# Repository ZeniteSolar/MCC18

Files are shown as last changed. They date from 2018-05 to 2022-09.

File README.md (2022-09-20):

# MCC18
Solar panel MPPT, cuk converter, with microcontroller 

# Procedimento de testes - MCC18

 - [Inspeção](#inspeção)
 - [Disgnostico Inicial](#diagnóstico-inicial)
 - [Diagnostico Preventivo](#diagnostico-preventivo)
 - [Teste Geral](#teste-geral)
    - [Entrada e saída de potencia](#entrada-e-saída-da-potência)
    - [Funcional](#funcional)
 - [Testes Individuais](#testes-individuais)
    - [Signals](#signals)
    - [MCC CAN Shield](#mcccanshield) 
 - [Driver](#driver)
    - [Esquematico](#esquemático)
    - [Reparos Obrigatorios](#reparos-obrigatórios)
    - [Verificando funcionamento](#verificando-se-está-funcionando)
    - [Correção de falhas](#correção-de-falhas)
        - [Se não houver sinal retangular na saída](#se-não-houver-sinal-retangular-na-saída)
        - [Se não houver +15V e -5V](#se-não-houver-15v-e--5v)
        - [Se não houver tensão em um dos barramentos de +15V ou -5V](#se-não-houver-tensão-em-um-dos-barramentos-de-15v-ou--5v)
        - [Se tem tensão no barramento, mas não tem sinal em gate e source](#se-tem-tensão-no-barramento-mas-não-tem-sinal-em-gate-e-source)

**Importante**: 
<span style="color:red">
NÃO TROCAR COMPONENTES ENTRE AS PLACAS, CADA MCC TEM SEU MCC_CAN_SHIELD, E CADA MCC_CAN_SHIELD TEM  SEU ATMEGA! 
SOMENTE REGRAVAR FIRMWARE EM ÚLTIMO CASO!
SEMPRE USAR LIMITE DE CORRENTE NAS FONTES!
SEMPRE LIMPAR EM BAIXO DO PLÁSTICO DOS CONECTORES BARRA_PINO!
</span>

Também Importante: Esse documento está escrito em ordem sequencial de testes, deve ser lido atentamente, pois um procedimento errado poderá causar danos permanentementes ao sistema, e as vezes difíceis de serem compreendidos.

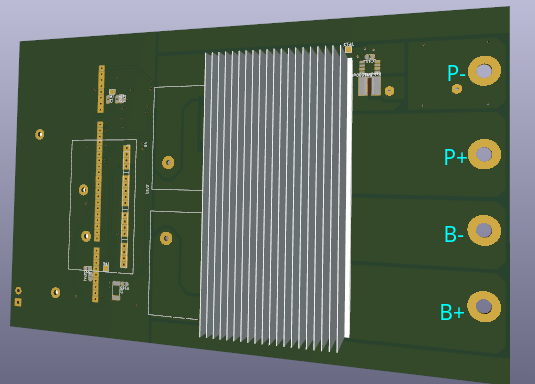
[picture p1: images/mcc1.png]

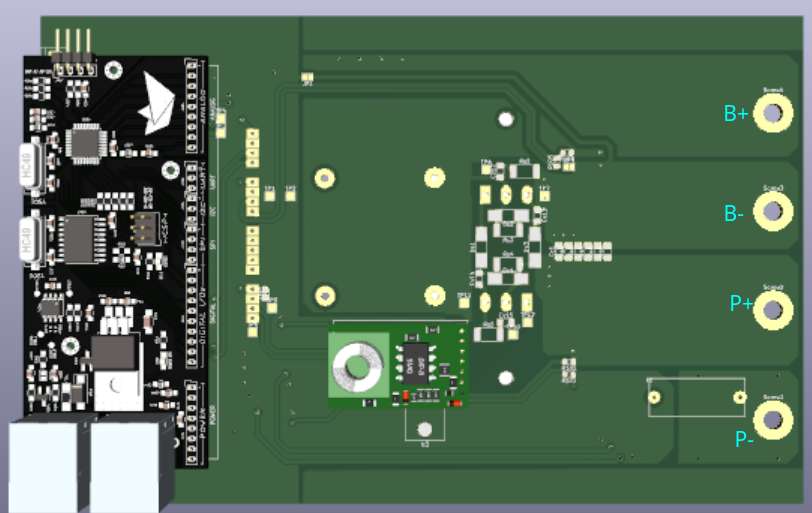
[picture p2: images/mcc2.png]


## INSPEÇÃO
Antes de mais nada, limpeza com álcool e escova, mas especialmente em baixo das barras de pino, pois costumam acumular sujeira em baixo, entre o plástico preto e o cobre, eles podem ser levantados/retirados com uma pinça, fazendo uma alavanca, ou com um alicate universal.
Inspeção visual na placa inteira, especialmente por resíduos e manchas, que podem dar dica sobre onde pode existir problemas. Outro ponto de se observar são trilhas rompidas, componentes rachados ou com aspecto estranho.

## DIAGNÓSTICO INICIAL
Desconectar MCC_CAN_SHIELD, SIGNALS e DRIVER, bem como qualquer elemento externo a placa, como fontes de tensão.

Multímetro: entre B+ e P-, resistência dos indutores, na faixa de mOhms, se tiver alta impedância:
 - Um dos indutores em aberto
 - Shunt em aberto

Multímetro: entre P+ e P-, observar a carga do capacitor, um curto pode ser:
 - Capacitor do painel em curto
 - Mosfet em curto drain-source
 - Capacitor de acoplamento e diodo em curto
 - Capacitor de acoplamento e capacitor da bateria em curto

Multímetro: entre B+ e B-, observar a carga do capacitor, um curto pode ser:
 - Capacitor da bateria em curto
 - Diodo em curto
 - Capacitor de acoplamento em curto
 - Capacitor de acoplamento e capacitor do painel em curto

Multímetro: entre P+ e B-, observar a carga do capacitor de acoplamento, um curto pode ser:
 - Capacitor de acoplamento em curto
 - Diodo e Mosfet em curto

Multímetro: verificar se gate-source ou gate-drain não estão em curto.

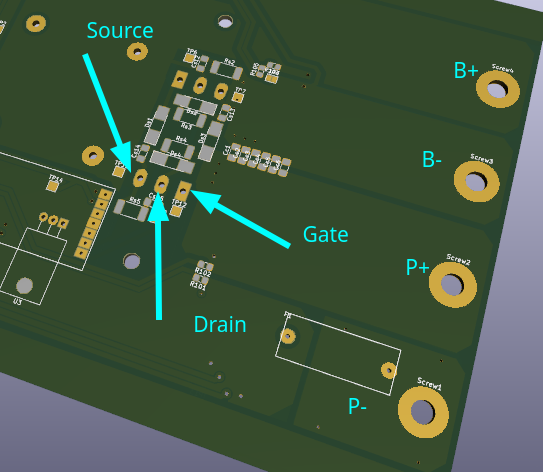
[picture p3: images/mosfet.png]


## DIAGNOSTICO PREVENTIVO

IMPORTANTE, este diagnostico SOMENTE pode ser feito quando se tem certeza de que não houve um mal funcionamento do modulo, por exemplo o modulo ficou em repouso por um tempo e quer verificar o funcionamento. Este teste estima que o modulo não tem nenhuma falha destrutiva, se houver duvidas é recomendável fazer o diagnostico inicial e teste geral antes!!!.

ATENÇÃO! Nunca efetuar o teste sem resistor de carga entre B+ e B- se em algum momento houver a desconexão do mesmo pode danificar o modulo!

 - Ligar uma Fonte CAN a uma fonte de laboratorio com a tensão entre 18 e 30V, limitada em 0.05A e verificar o consumo, se a fonte limitar em corrente examinar o MCC_CAN_Shield está queimado, se não limitar em corrente esperar uns segundos e os leds deveriam piscar alternadamente (talvez passado um tempo um led fique fixo e outro desligado, não tem problema), se não o MCC_CAN_Shield está com problema.
 
 **(Sempre que for ligar uma placa no MCC desligar a fonte CAN (Se estiver usando uma fonte de laboratorio não desligue ela, desconecte o fio que alimenta o circuito é mais seguro))**

 - Com o MCC_CAN_Shield funcionando conecta-lo no MCC e aumentar o limite de corrente da fonte para 0.10A.
 - Conectar o driver e verificar o consumo, se limitar em corrente o driver está queimado, se não prosseguir.
 - Conectar a placa dos sensores, se limitar em corrente a placa está queimada, se não prosseguir.
 - **PASSO MUITO IMPORTANTE** Conectar o resistor de carga (valor máximo: 25R, recomendável: 20R, mínimo: 1R) entre B+ e B-
 - Ligar outra fonte (deve estar isolada) com a tensão em 0V e a corrente limitada a 0.05A entre +P e -P.
 - Medir a tensão de saída
 - Fazer uma rampa na fonte conectada em P+ e P- de 0V até 7V e de 0.05A até 1A (fazer devagar), enquanto faz a rampa a tensão de saída deveria aumentar se não aumentar e a fonte sempre ficar limitando em corrente, tem problema na parte de potencia, se a tensão de saída não aumentar e não houver consumo ou o driver ou a parte de potencia não funcionam
 - Se houve tensão na saída, a fonte de P+ e P- deveria ficar oscilando entre limite de corrente e limite de tensão e os LEDs da placa de controle deveriam estar alternando. Se não for o caso, desconectar o cabo RJ45 e conectar novamente, se mesmo assim depois de uns 30 segundos não ficar oscilando entre o limite de corrente e o limite de tensão, provavelmente algum sensor deve estar queimado.
 - Para diagnosticar o sensor conectar um Arduíno nos pinos de dados e na serial verificar se os valores medidos condizem com os que aparecem na fonte de P+ e P-.

## TESTE GERAL
Primeiro teste a ser realizado após limpeza e inspeção visual. Esse teste garante que as chaves e capacitores de potência estejam sem fuga de corrente para os níveis de tensão de trabalho nominal. Caso haja fuga de corrente, pode-se optar por aumentar o nível da corrente e localizar a fuga pela elevação de temperatura. 

<span style="color:red"> Importante: Obrigatório o uso de óculos de proteção.</span>

### Entrada e Saída da potência

Nesta etapa testamos o isolamento da placa, a capacidade dos capacitores de suportar a tensão, bem como dos indutores, trilhas, fusível e shunt de suportar a corrente.

 - Desenconectar o MCC_CAN_SHIELD, DRIVER e SIGNALS
 - Fazer uma rampa de tensão de 0 a 50V @ 100mA entre B+ e B-
 - Fazer uma rampa de tensão de 0 a 30V @ 100mA entre P+ e P-
 - Fazer uma rampa de tensão de 0 a 100V @ 100mA entre P+ e B-
 - Fazer uma rampa de corrente de 0 a 10A @ 1V entre B+ e P-

### Funcional
**Alimentação e CIs possivelmente vivos**

 - Remover o atmega do MCC_CAN_SHIELD
 - Conectar o MCC_CAN_SHIELD, ligar o cabo CAN, verificar baixo consumo
 - Medir tensão de 5V

**Geração de PWM e sinal de vida**

 - Conectar o atmega no MCC_CAN_SHIELD
 - Conectar o conector da rede CAN, verificar baixo consumo de corrente
 - Conectar USB/SERIAL para monitorar a serial, deve observar ‘Início com sucesso’
 - Deve haver o surgimento de sinal pwm no pino do conector onde o driver fica encaixado, assim como o aumento da variável de duty cycle pela serial. Talvez a verificação dos limites mínimos para funcionamento esteja ativa, nesse caso, precisa adicionar fontes na entrada e saída.
 - Remover fontes externas, conectar driver, verificar baixo consumo
 - <span style="color:red"> SEM ATERRAMENTO </span>, Medir Vgs, deve haver o mesmo sinal de pwm, de -5 a 15V @ 100kHz.

**Leitura de sinais de tensão**
 - Remover alimentação, conectar SIGNALS, MCC_CAN_SHIELD (com atmega)
 - Remover o DRIVER
 - Conectar USB/SERIAL para monitorar a serial
 - Fazer uma rampa de tensão de 0 a 30V @ 100mA entre P+ e P-:
    - Observar mudança na variável Vp
 - Zerar fonte de tensão:
    - Observar mudança na variável Vp
 - Fazer uma rampa de tensão de 0 a 50V @ 100mA entre B+ e B-:
    - Observar mudança na variável Vb
 - Zerar fonte de tensão:
    - Observar mudança na variável Vb

**MPPT e leitura de sinal de corrente**
 - Remover alimentação, conectar SIGNALS, MCC_CAN_SHIELD (com atmega), e DRIVER
 - Conectar USB/SERIAL para monitorar a serial
 - Resistência de carga no B+ e B-, pode ser na faixa de 100 Ohms
 - Fazer uma rampa de corrente de 1A @ 10V entre P+ e P-:
    -  <span style="color:red"> CUIDADO: </span> tensão na saída não deve ultrapassar 50V, se a carga for desconectada, capacitores podem explodir e sensor de corrente queimar.
 - observar busca pelo ponto de máxima potência
 - observar mudança na variável Ip

**MPPT com potência**
 - Ainda sem dissipador e com o mesmo setup anterior, reduzir a resistência e aumentar a tensão e corrente na entrada até 5A na entrada
 - Montar dissipador, e com o mesmo setup, chegar até 8A na entrada.

### TESTES INDIVIDUAIS
A SER REALIZADO CASO FALHE EM ALGUM TESTE GERAL.

#### SIGNALS

 - Alimentação:
    - Alimentar placa com 5V pela barra de pinos
    - Injetar sinal de tensão em cada pino de entrada de sinal da placa e verificar se a tensão nos pinos de saída.
 - Sensores:
    - Remover Atmega
    - Alimentar a placa com o conector do CAN
    - Botar sinal em cada pino do conector de ADC da placa e verificar se a tensão no MCU está correta

#### MCC_CAN_SHIELD

 - Alimentação:
    - Remover atmega
    - Alimentar a placa com o conector do CAN
    - Verificar baixo consumo de corrente
    - Verificar tensão de 5V
 - Sensores:
    - Remover Atmega
    - Alimentar a placa com o conector do CAN
    - Injetar sinal de tensão em cada pino do conector de ADC da placa e verificar se a tensão no MCU está correta
 - Atmega328:
    - Verificar pinos de alimentação do atmega (todos abaixo de 5V
    - Colocar atmega
    - Alimentar a placa com o conector do CAN
    - Verificar clock e reset do atmega
 - CAN:
    - Colocar atmega
    - Alimentar a placa com o conector do CAN
    - Verificar clock do MCP2515
    - Verificar clock na SPI
    - Verificar RX (entre MCP2515 e MCP2551), deve ter alguma coisa
    - Verificar TX (não deve ter sinal)
    - Verificar CAN_H e CAN_L, devem ter sinal se tiver sinal no RX ou TX
 - Funcionamento:
    - Colocar Atmega
    - Alimentar a placa com o conector do CAN
    - Verificar baixo consumo de corrente
    - Conectar na serial e ler as mensagens

### DRIVER

Procedimento de Reparo do Driver Isolado INEP
IMPORTANTE
<span style="color:red"> Para testar o driver é muito importante que todos os equipamentos estejam isolados com transformador isolador, já que ao ser um driver isolado qualquer tensão aplicada pela rede pode acabar queimando os componentes do mesmo.
Para reduzir riscos de ESD é importante colocar um resistor de alto valor entre o gnd e o source do Mosfet.
</span>

### ESQUEMÁTICO:

https://drive.google.com/drive/u/0/folders/0B_EOV_z-bdXUR3FXRHJyZm9FUkE?resourcekey=0-0dKXDxxFrtL1GblLArqhaQ

**Pinagem:**

<span style="color:red">Muito cuidado que este driver pode ser soldado nos dois sentidos sempre verificar onde está a bobina</span>

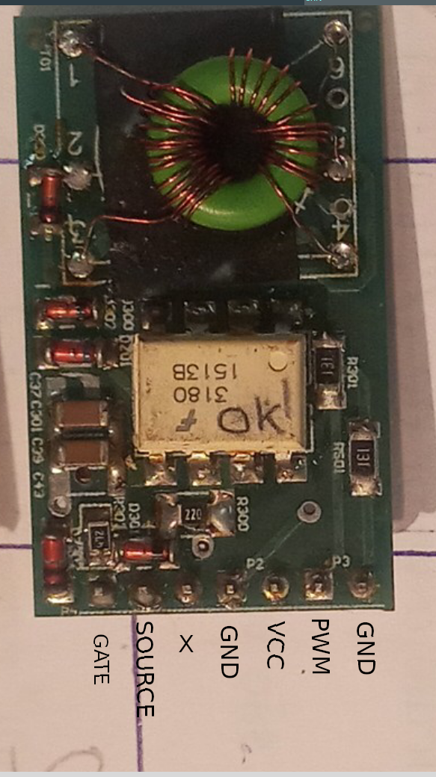
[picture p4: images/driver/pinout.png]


### Esquemático teste:

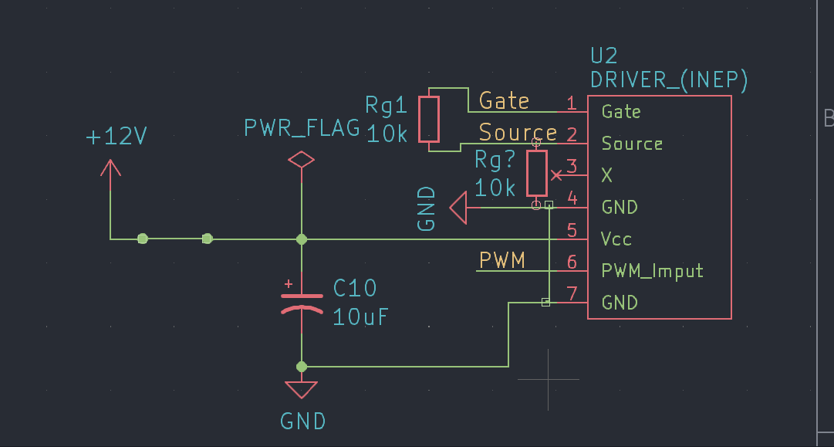
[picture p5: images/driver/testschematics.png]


#### Reparos obrigatórios:
 
 - Trocar R80 para um resistor de 72 ohms
 - Trocar C28 por um capacitor de 1nF
 - Trocar RS01 e R301 por resistores de 220R

#### Verificando se está funcionando:

 - Antes de tudo fazer inspeção visual se todos os componentes estão nos seus devidos lugares 
 - Conectar o driver em uma protoboard e NÃO ESQUECER DE USAR TODOS OS EQUIPAMENTOS ISOLADOS E TER MUITO CUIDADO COM AS REFERENCIAS.
 - Conectar os dois resistores do esquemático e Colocar uma fonte limitada a 0.1A de 12V entre +12V e gnd (esquemático) e verificar o consumo de corrente, se está próximo aos (tem que medir) pode prosseguir com o teste se não ir para a etapa de correção de falhas.



 - Colocar um gerador de funções com 2.5V de amplitude e 2.5V de offset em 100khz e sinal retangular entre PWM e GND (não esquecer de conectar os dois GNDs) (é normal aumentar levemente o consumo)  e com um osciloscópio verificar se tem um sinal retangular entre gate e source de 100khz e Vmax de +15 e Vmin de  -5V. Se sim o driver pode ser testado em um controlador de carga. Se não vai ter que ir para a etapa de correção de falhas. 

#### Correção de falhas:
- Comportamentos:
#### Se não houver sinal retangular na saída
 - Verificar se tem +15V com a ponteira comum do multímetro no pino 4 do indutor e a vermelha no catodo do D300(localizado na proxima imagem)
 - Verificar se tem -5V com a ponteira comum do multímetro no pino 4 do indutor e a vermelha no anodo do D302(localizado na próxima imagem)
    
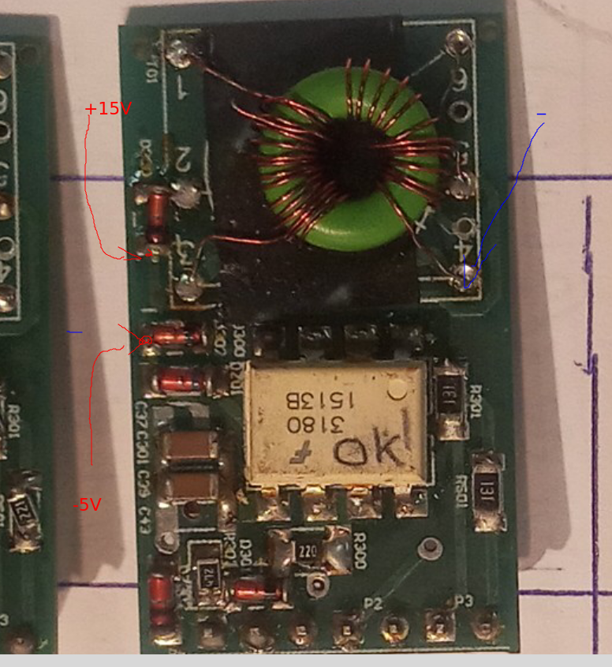
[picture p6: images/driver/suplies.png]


##### Se não houver +15V e -5V:
- Desconectar R80
 aplicar 12V em +12V e em GND (esquemático), colocar o osciloscopio com a referencia em GND e a ponteira no retângulo rosa da próxima imagem(pino 3 do 555 ou em R80) deveria ter uma sinal retangular de 250khz) se não houver o problema está no circuito do 555

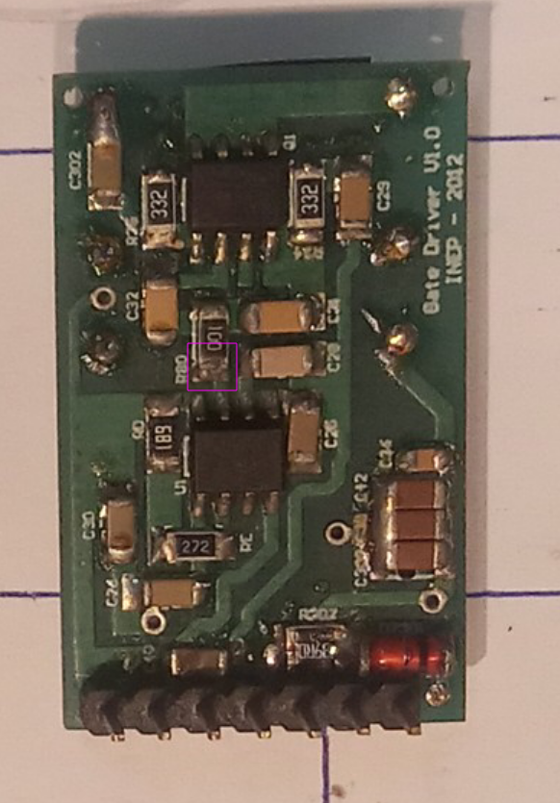
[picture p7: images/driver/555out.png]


 - Se houver sinal retangular o circuito do 555 está correto
 - Medir com o multímetro em tensão de junção (diodo) com a ponteira preta no pino 7 ou 8 de Q1 e com a vermelha no pino 1 deveria ter aproximadamente 0.7V, se estiver em 0 ou em circuito aberto significa que o Q1 está queimado,

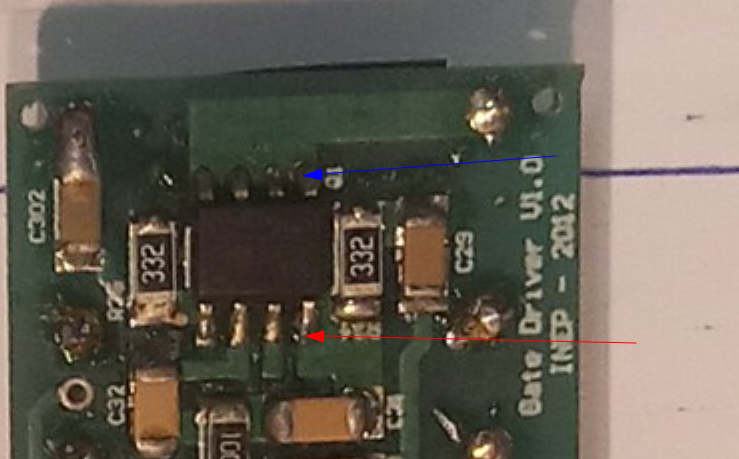
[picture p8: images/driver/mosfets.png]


 - Medir com o multimetro em tensão de junção (diodo) com a ponteira preta no pino 3 de Q1 e com a vermelha no pino 5 ou 6 deveria ter aproximadamente 0.7V, se estiver em 0 ou em circuito aberto significa que o Q1 está queimado, 

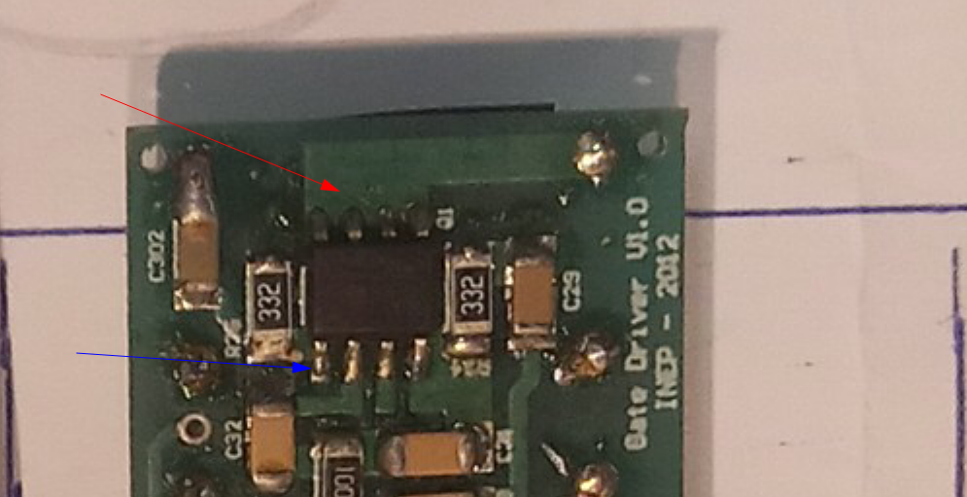
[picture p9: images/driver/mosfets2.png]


 - logo passar para as verificações do caso de Se não houver tensão em um dos barramentos de +15V ou -5V
 - Se nenhum desses procedimentos solucionarem , trocar Q1 (não esquecer de conectar R80) e verificar se volta a ter tensão em +15 e -5 
 
##### Se não houver tensão em um dos barramentos de +15V ou -5V
 - Medir com o multímetro em tensão de junção (diodo) e verificar se D300 e D302 estão funcionando corretamente, se não trocar
 - Medir com o multímetro em escala de ohms, entre o barramento (+15V e -5V) e GND, se houver curto em um unico barramento provavelmente seja C300, C42, C36, C38 para +15V em curto, C301, C37, C39, C43 para -5V em curto. 
 - Medir em tensão de junção (diodo) entre -5V (vermelha) e +15V (preta) deveria estar próximo dos 0.7V se não estiver DZ01 está com falha.
 - Medir entre o pino 5 e 2 da bobina com o multímetro em ohms, deveria estar proximo dos 0ohms, se estiver em circuito aberto significa que a bobina está mal soldada ou com enrolamento cortado.

##### Se tem tensão no barramento, mas não tem sinal em gate e source
 - Medir com o multímetro em tensão de junção entre os pinos 2 e 3 do U300, deveria ter aproximadamente 1.2V se não tem provavelmente U300 está queimado.

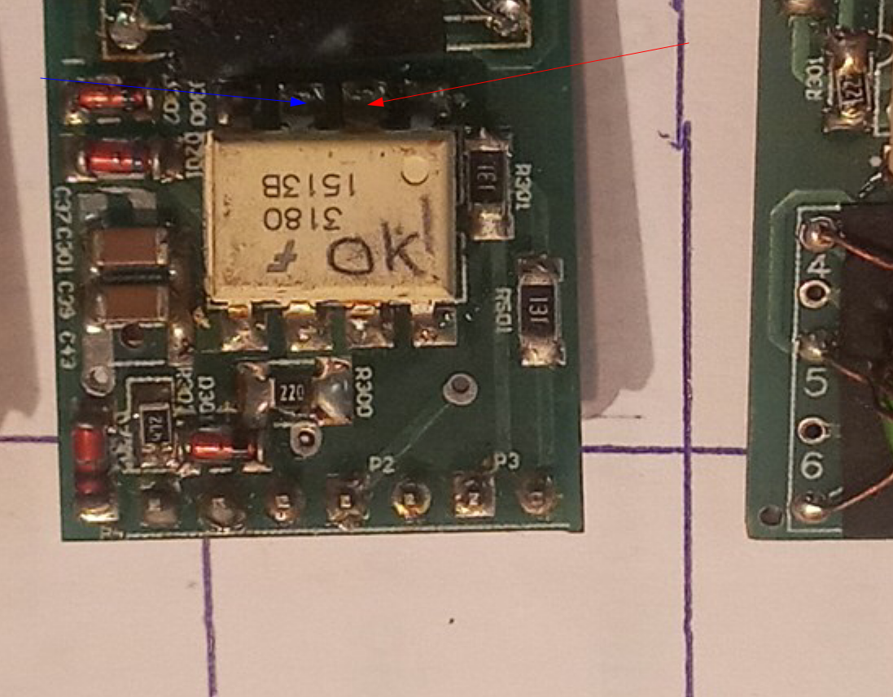
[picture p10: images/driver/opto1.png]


 - Medir entre o pino 6 ou 7 do U300 e o source do driver, com o multímetro em ohms, deveria ter aproximadamente 4.7k, se não tiver provavelmente DZ301 ou DZ302 estão queimados, ou também R303 ou R302 ou R300.
 - Com uma fonte limitada a 0.03A, com 20V conectar o positivo em +15V (catodo D300) e o negativo em -5V (anodo do D302), colocar um gerador de funções com sinal retangular offset de 2.5V, amplitude de 2.5V e frequencia de 100khz entre pwm e GND e um resistor de 10k entre GND e -5V. Medir com osciloscópio com a referencia no GND da fonte e com a ponteira no pino 6 ou 7 do U300, deveria ter um sinal retangular de 0 a 20V, se não houver ou se a fonte limitar provavelmente U300 está queimado, se houver testar trocando Q1 e ver se o driver funciona, se não provavelmente o driver está possuído, melhor ir para o proximo

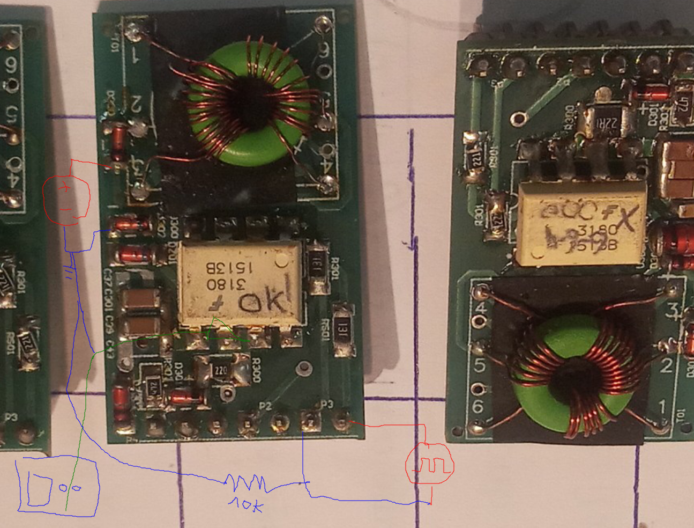
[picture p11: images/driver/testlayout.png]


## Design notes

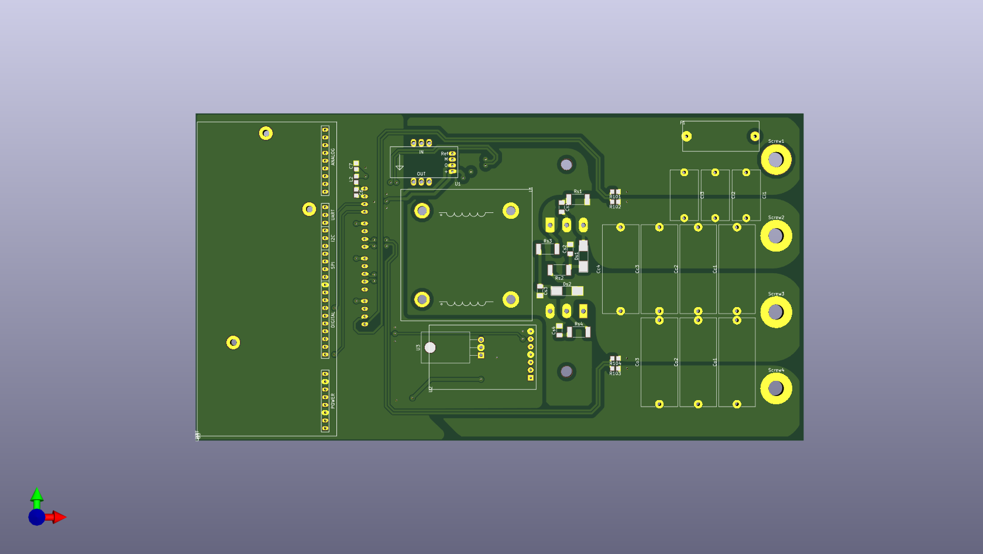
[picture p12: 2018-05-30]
Hardware/Hall_sensor/Cuk_converter/KiCad/IMG/back.PNG

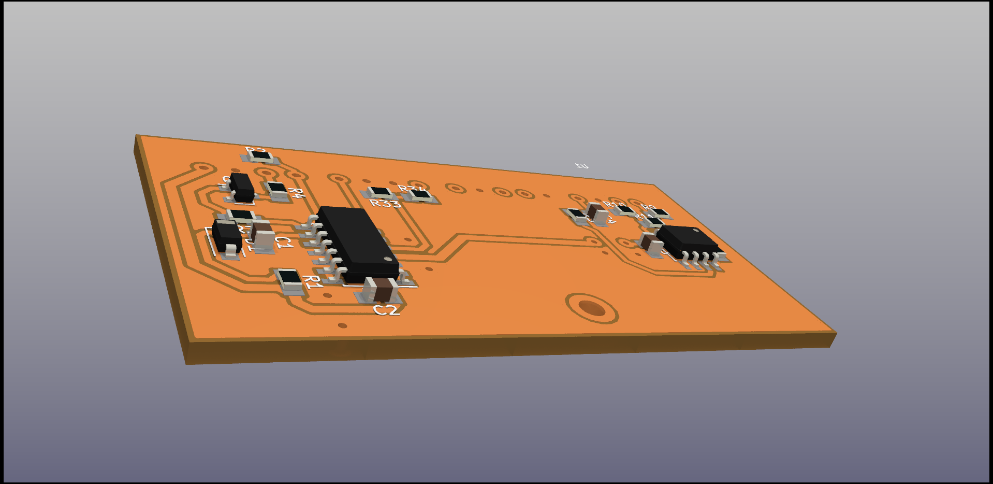
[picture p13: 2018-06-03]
Hardware/Shunt_sensor/Signals/IMG/angled.png

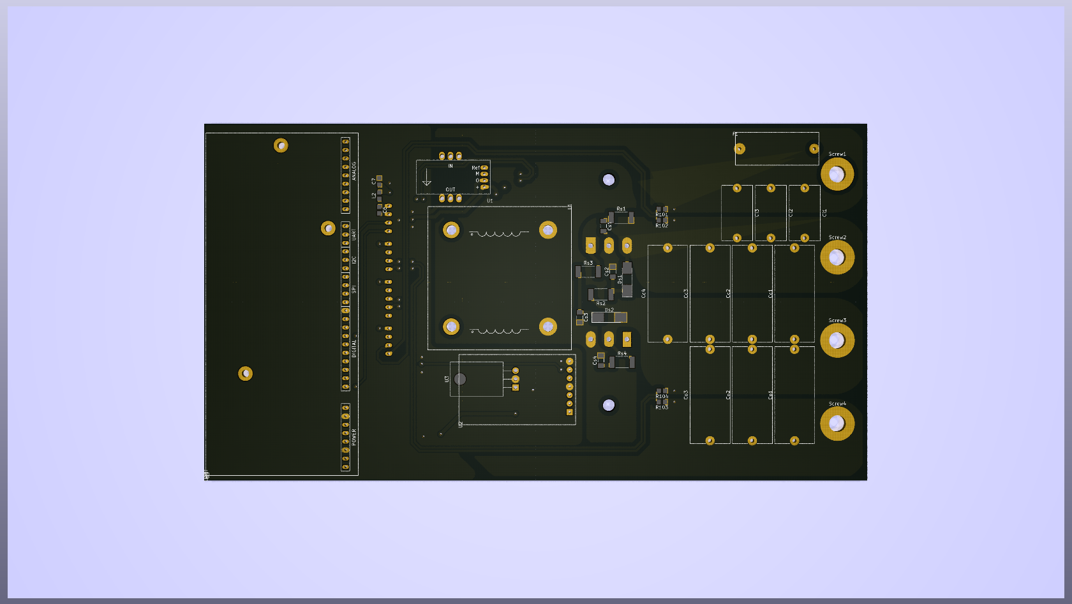
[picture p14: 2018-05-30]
Hardware/Hall_sensor/Cuk_converter/KiCad/IMG/front.PNG

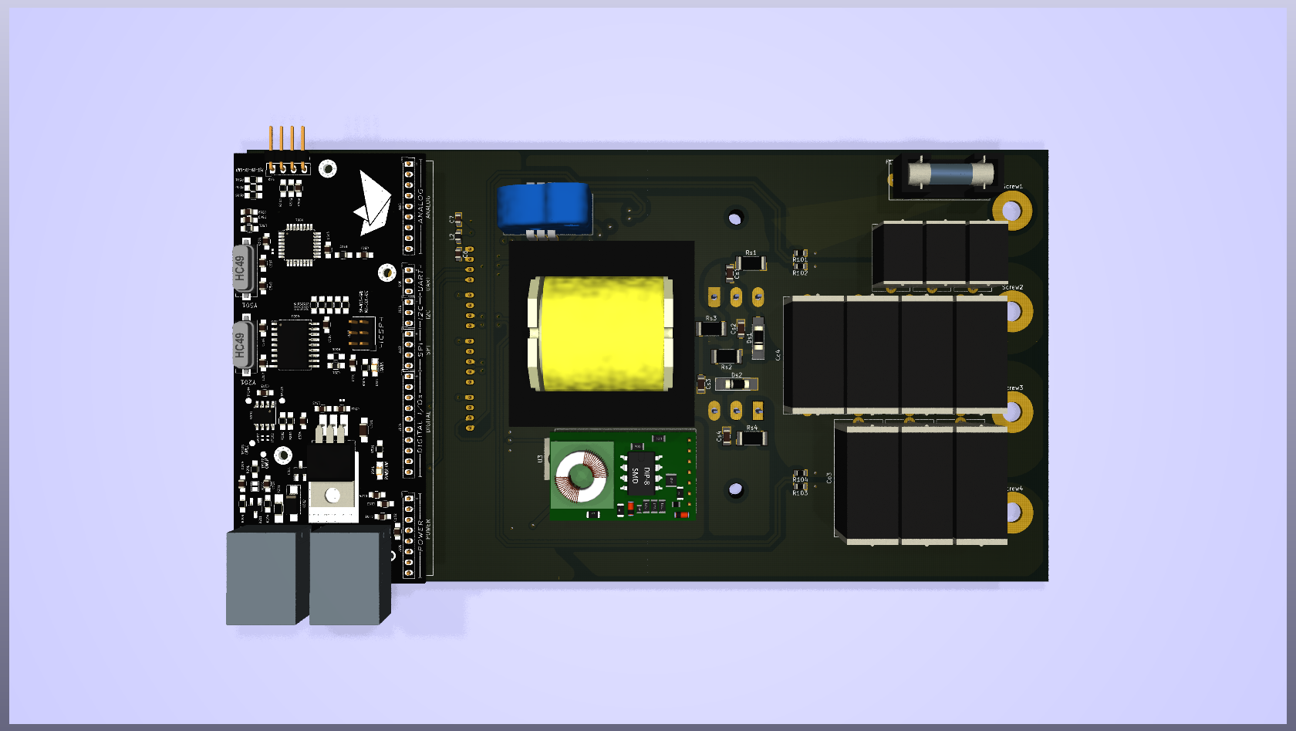
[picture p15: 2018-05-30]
Hardware/Hall_sensor/Cuk_converter/KiCad/IMG/front_populated.PNG

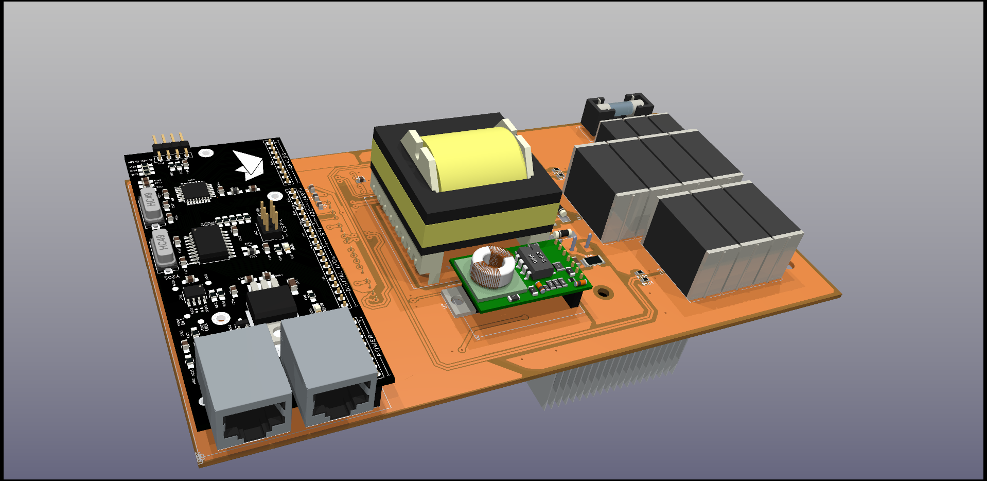
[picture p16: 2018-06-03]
Hardware/Shunt_sensor/Cuk_converter/KiCad/IMG/angled.PNG

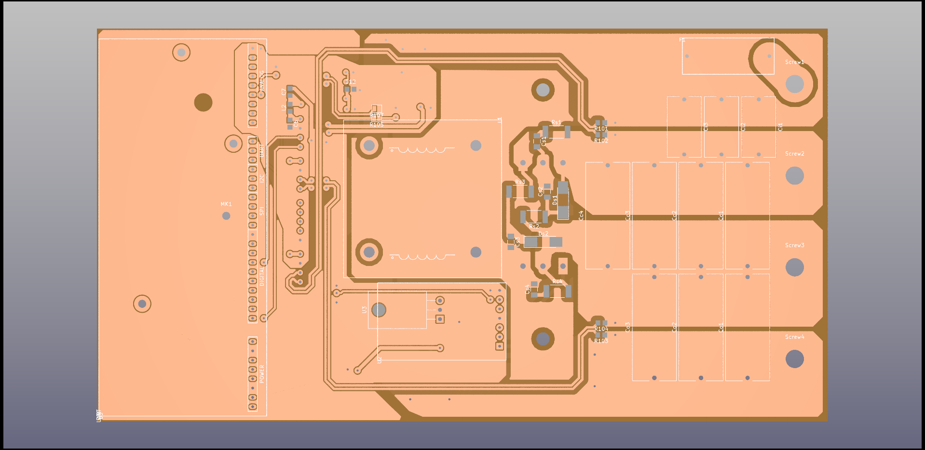
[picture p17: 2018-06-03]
Hardware/Shunt_sensor/Cuk_converter/KiCad/IMG/front.PNG

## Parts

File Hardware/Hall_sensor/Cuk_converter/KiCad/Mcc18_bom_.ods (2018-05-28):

Component | Description | Part | References | Value | Footprint | Quantity p/PCB | Datasheet | Tolerance | Type | Voltage | Power
1 | Unpolarized capacitor | C_Small | C1 C3 C4 C6 C7 C8 C9 | 100nF | C_0805_2012Metric_Pad1.29x1.40mm_HandSolder | 7
2 | Polarised capacitor | CP1_Small | C2 C5 C10 | 10uF | C_0805_2012Metric_Pad1.29x1.40mm_HandSolder | 3
3 | Unpolarized capacitor | C | Cc1 Cc2 Cc3 Cc4 | 6.8uF | C_Rect_L29.0mm_W11.9mm_P27.50mm_MKT | 4
4 | Unpolarized capacitor | C | Ci1 Ci2 Ci3 | 4.7uF | C_Rect_L16.5mm_W9.2mm_P15.00mm_MKT | 3
5 | Unpolarized capacitor | C | Co1 Co2 Co3 | 4.7uF | C_Rect_L29.0mm_W11.9mm_P27.50mm_MKT | 3
6 | Unpolarized capacitor | C_Small | Cs1 Cs2 Cs3 Cs4 | ?? | C_1206_3216Metric_Pad1.39x1.80mm_HandSolder | 4 |  | 10% | X7R | 200V
7 | Schottky diode, two anode pins | D_Schottky_AKA | D1 | 80CPQ150PbF | TO-247-3_Horizontal_TabUp | 1 | https://www.vishay.com/docs/94257/vs-80cpq150.pdf
8 | Diode, small symbol | D_Small | Ds1 Ds2 | BYD77 | D_MELF_Handsoldering | 2 | https://media.digikey.com/pdf/Data%20Sheets/NXP%20PDFs/BYD77.pdf
9 | Fuse, generic | Fuse | F1 | Fuse | Porta_Fusivel | 1
10 | Heatsink | Heatsink | HS1 | Heatsink | hs10425 | 1
11 | Coupled inductor with Iron Core | L_Core_Iron_Coupled | L1 | 50uH/50uH | NEE-42-20-DE | 1
12 | Inductor, small symbol | L_Small | L2 L3 | L_Small | L_0805_2012Metric_Pad1.29x1.40mm_HandSolder | 2
13 | 30A Id, 50V Vds, N-Channel Power MOSFET, TO-220 | IRF540N | Q1 | IRFP4321PbF | TO-247-3_Horizontal_TabUp | 1 | https://www.infineon.com/dgdl/irfp4321pbf.pdf?fileId=5546d462533600a40153562c4f802011
14 | Resistor, small symbol | R_Small | R1 | 10k | R_0805_2012Metric_Pad1.29x1.40mm_HandSolder | 1
15 | Resistor, small symbol | R_Small | Rs1 Rs2 Rs3 Rs4 | ?? | R_2512_6332Metric_Pad1.49x3.40mm_HandSolder | 4 |  | 10% |  |  | 1W
16 |  | DRIVER_(INEP)-Driver_FET-Mcc18-rescue-Mcc18-rescue-Mcc18-rescue-Mcc18-rescue-Mcc18-rescue | U2 | DRIVER_(INEP) | Driver_(INEP) | 1
17 | Positive 1A 35V Linear Regulator, Fixed Output 5V, TO-220 | LM7812_TO220 | U3 | LM7812_TO220 | TO-220-3_Horizontal_TabDown | 1 | http://www.fairchildsemi.com/ds/LM/LM7805.pdf
18 |  | LTSP_25-NP-Sensor_Current-Mcc18-rescue-Mcc18-rescue-Mcc18-rescue-Mcc18-rescue-Mcc18-rescue | U1 | LTSP_25-NP | LTSP_25-NP | 1
19 |  | Signals_MCC-MCC18 | U4 | Signals_MCC | Signals | 1
20 |  | ZCS-ZCS-Mcc18-rescue | U5 | ZCS | ZCS18 | 1
Component Groups: | 20
Component Count: | 43
Fitted Components: | 43
Number of PCBs: | 1
Total components: | 43
Schematic Version:
Schematic Date:
BoM Date: | 28/05/2018 12:19:19
KiCad Version: | Eeschema (5.0.0-rc2-dev-586-g888c43477)

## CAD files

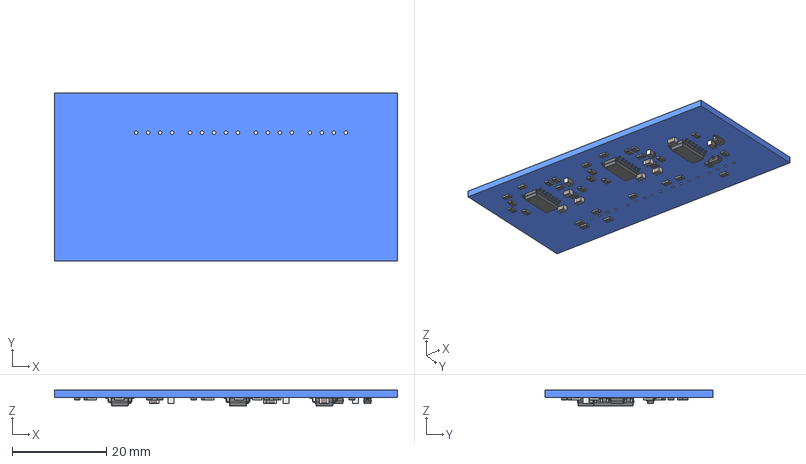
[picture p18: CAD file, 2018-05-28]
Hardware/Hall_sensor/Signals/Signal1.step
72.6 x 35.6 x 3.35 mm
Pcb
R_0805_2012Metric_
C_0805_2012Metric_
C_0805_2012Metric_001
C_0805_2012Metric_002
C_0805_2012Metric_003
C_0805_2012Metric_004
C_0805_2012Metric_005
C_0805_2012Metric_006
C_0805_2012Metric_007
C_0805_2012Metric_008
C_0805_2012Metric_009
D_SOD_123_
SOT_23_
R_0805_2012Metric_001
R_0805_2012Metric_002
R_0805_2012Metric_003
R_0805_2012Metric_004
R_0805_2012Metric_005
R_0805_2012Metric_006
R_0805_2012Metric_007
R_0805_2012Metric_008
R_0805_2012Metric_009
R_0805_2012Metric_010
R_0805_2012Metric_011
R_0805_2012Metric_012
R_0805_2012Metric_013
R_0805_2012Metric_014
R_0805_2012Metric_015
R_0805_2012Metric_016
R_0805_2012Metric_017
R_0805_2012Metric_018
R_0805_2012Metric_019
R_0805_2012Metric_020
R_0805_2012Metric_021
R_0805_2012Metric_022
R_0805_2012Metric_023
R_0805_2012Metric_024
R_0805_2012Metric_025
SOIC_14_39x87mm_P127mm_
R_0805_2012Metric_026
R_0805_2012Metric_027
R_0805_2012Metric_028
R_0805_2012Metric_029
R_0805_2012Metric_030
SOIC_14_39x87mm_P127mm_001
SOIC_14_39x87mm_P127mm_002

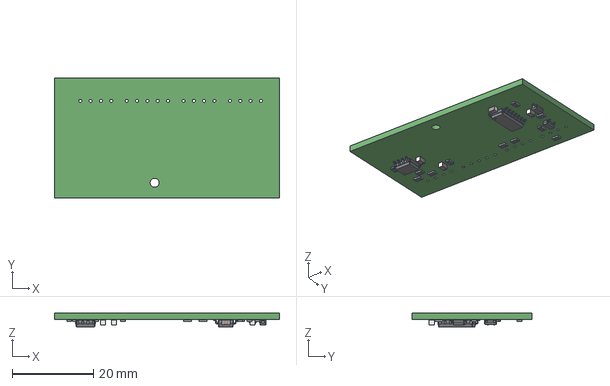
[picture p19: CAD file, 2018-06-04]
Hardware/Shunt_sensor/Signals/SignalShunt.stp
55.4 x 29.5 x 3.40 mm

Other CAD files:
Hardware/Hall_sensor/Signals/SignalPCB.stp
Hardware/Shunt_sensor/Signals/SignalPCB.stp
Hardware/Hall_sensor/Signals/Signal1.FCStd
Hardware/Shunt_sensor/Signals/Signal1.FCStd

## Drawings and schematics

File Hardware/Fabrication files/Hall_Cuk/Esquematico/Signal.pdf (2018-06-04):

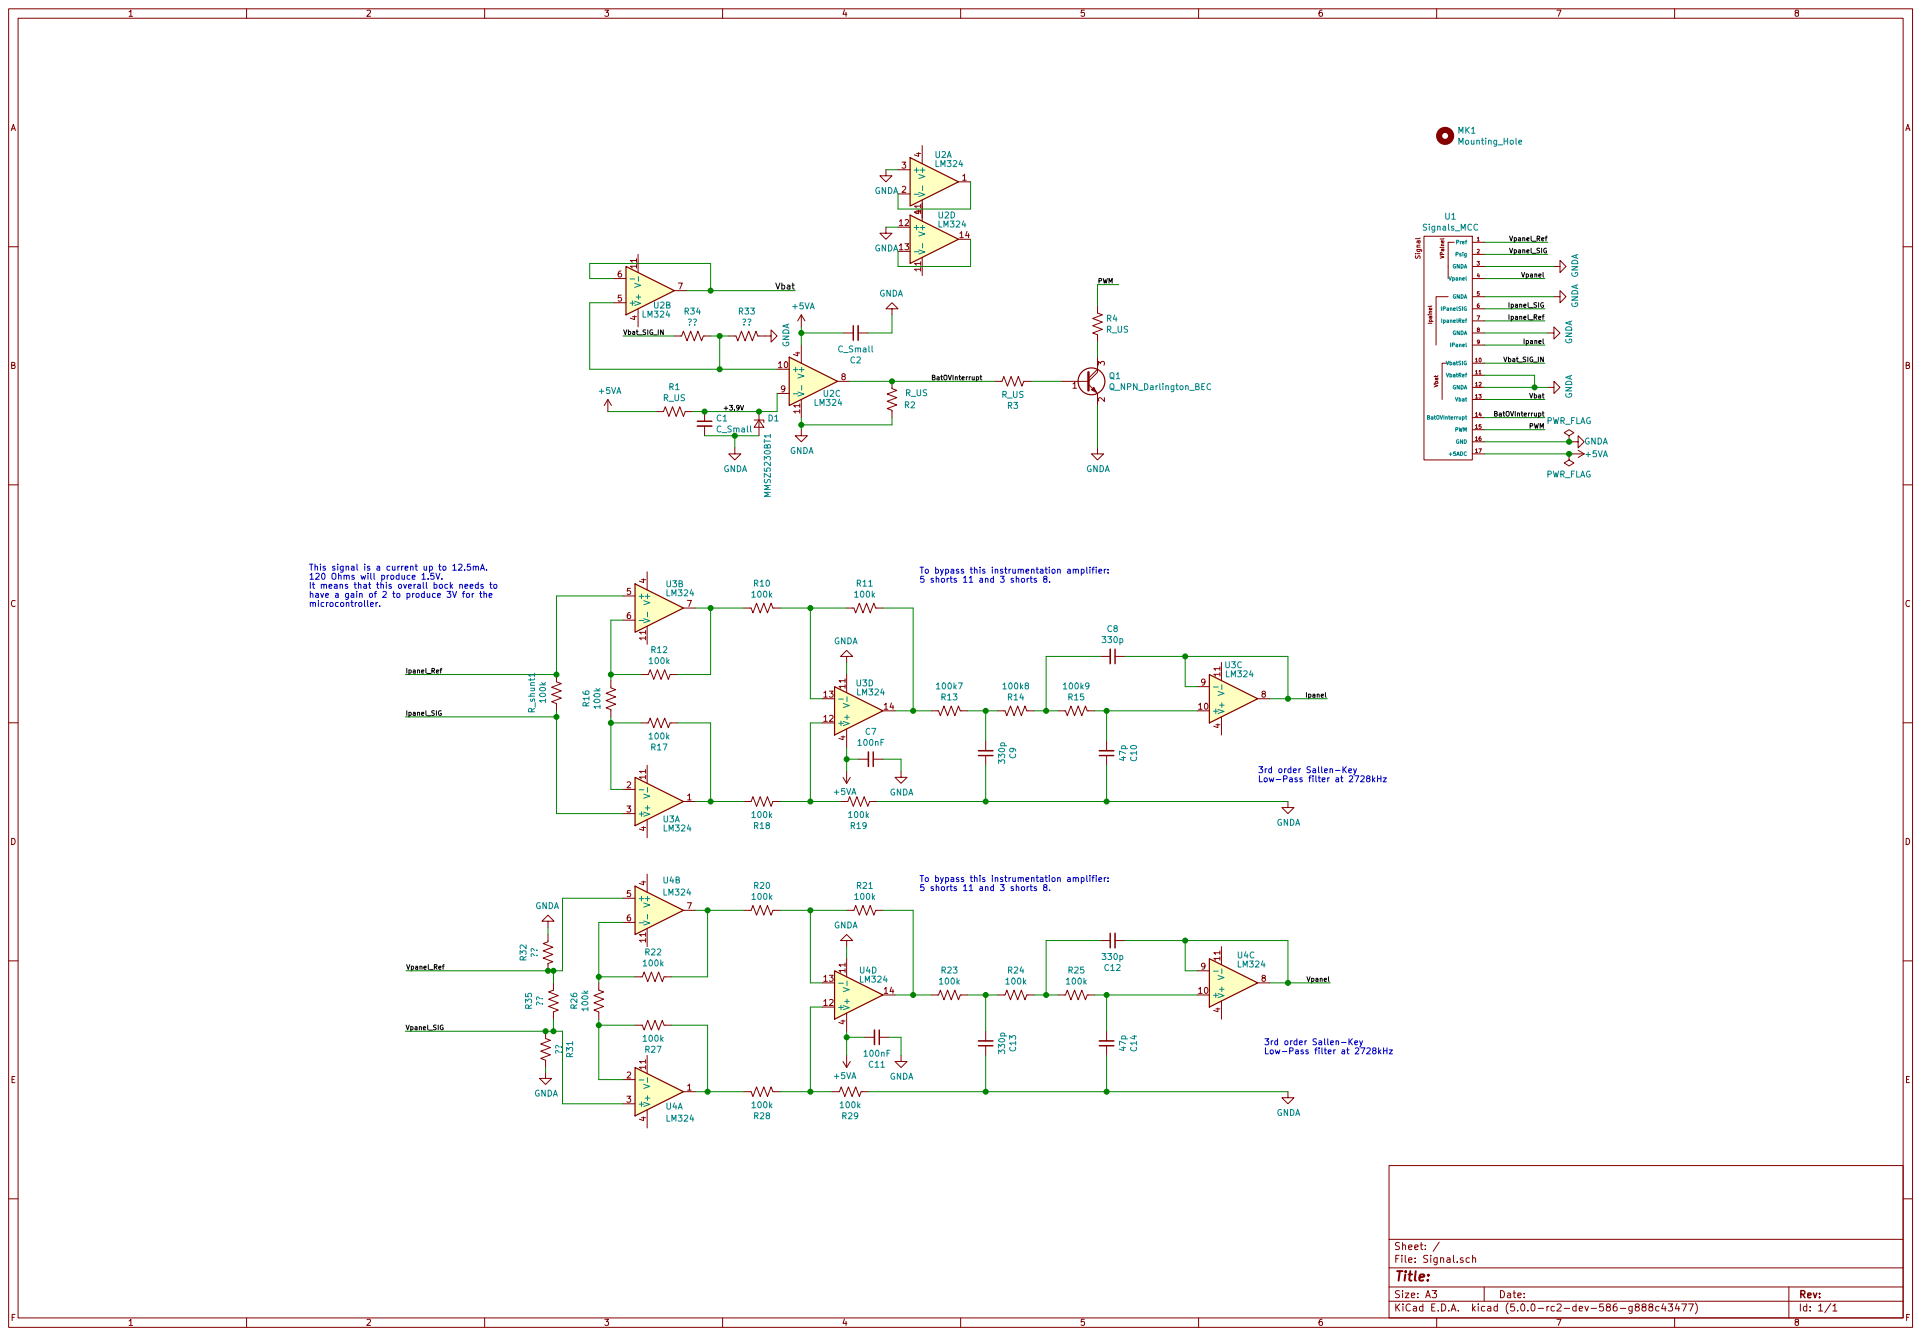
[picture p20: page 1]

File: Signal.sch Sheet: / V- 11 V+ 4 +

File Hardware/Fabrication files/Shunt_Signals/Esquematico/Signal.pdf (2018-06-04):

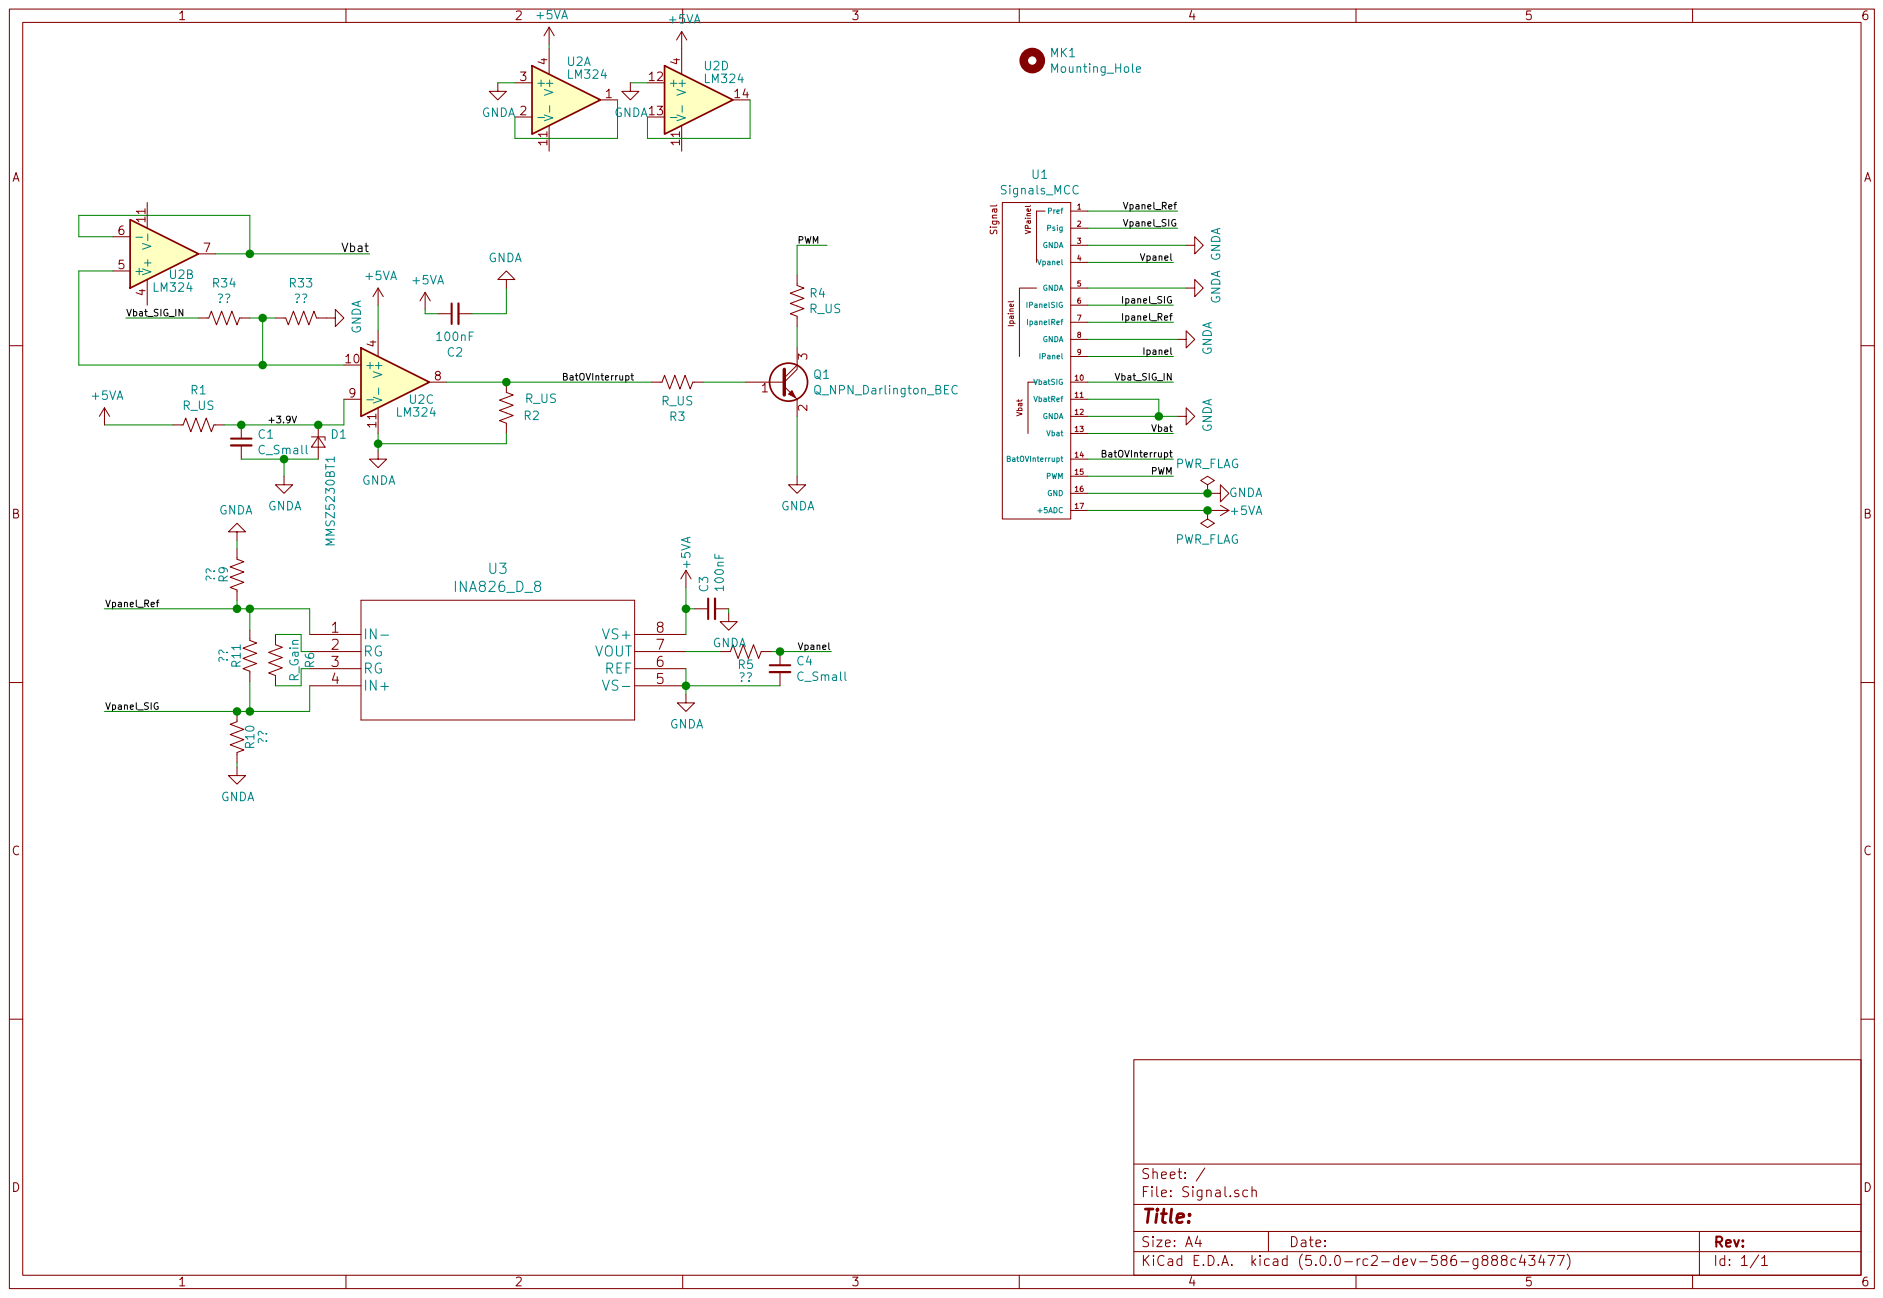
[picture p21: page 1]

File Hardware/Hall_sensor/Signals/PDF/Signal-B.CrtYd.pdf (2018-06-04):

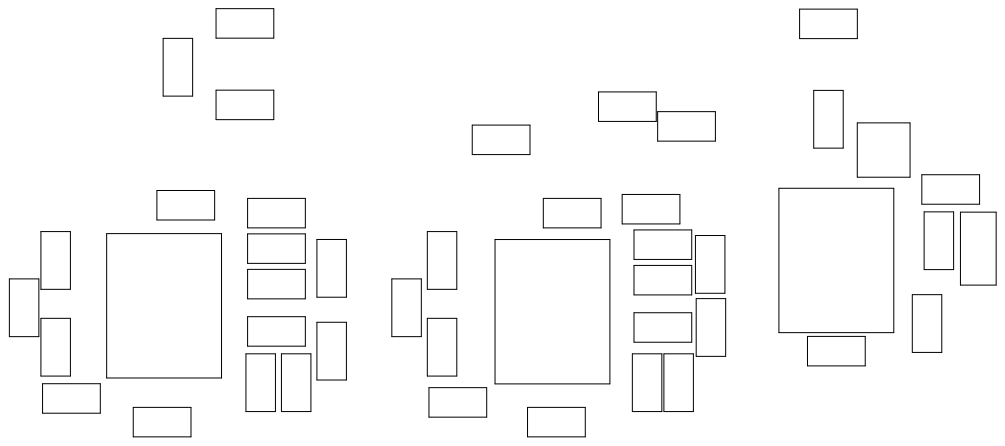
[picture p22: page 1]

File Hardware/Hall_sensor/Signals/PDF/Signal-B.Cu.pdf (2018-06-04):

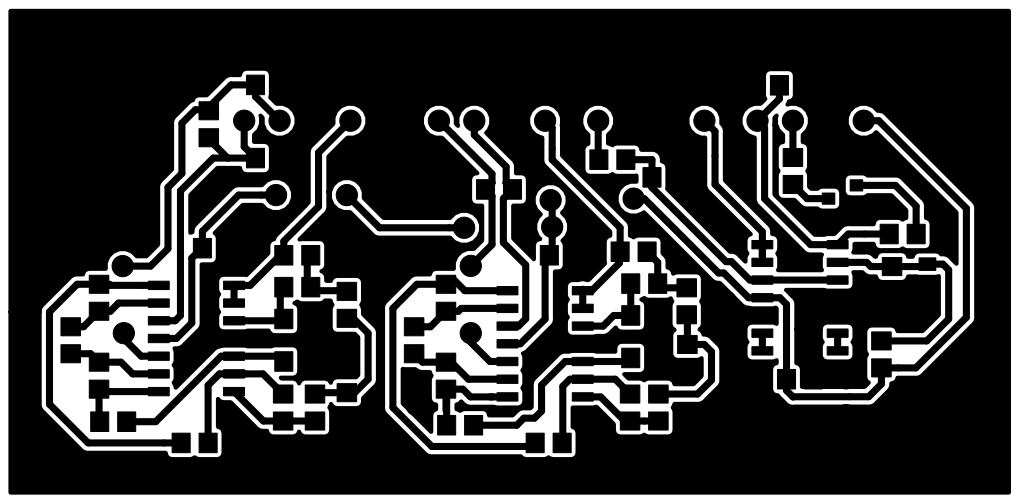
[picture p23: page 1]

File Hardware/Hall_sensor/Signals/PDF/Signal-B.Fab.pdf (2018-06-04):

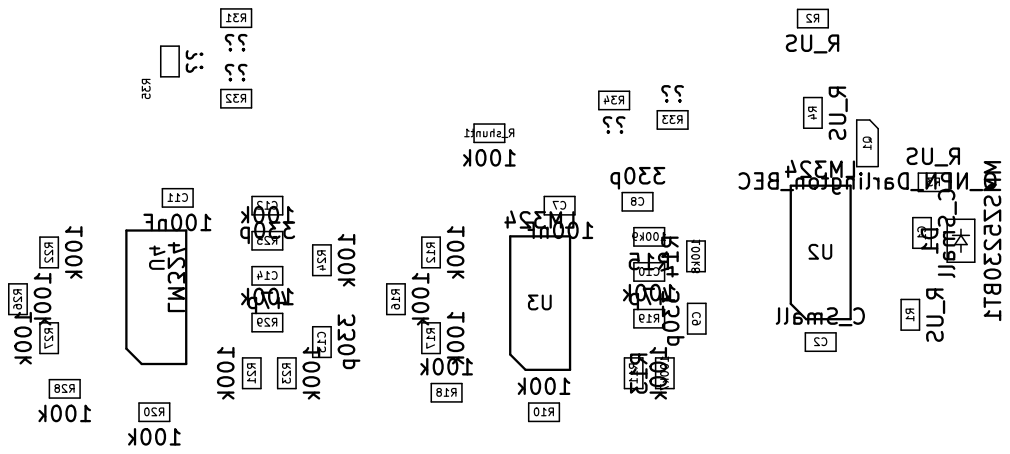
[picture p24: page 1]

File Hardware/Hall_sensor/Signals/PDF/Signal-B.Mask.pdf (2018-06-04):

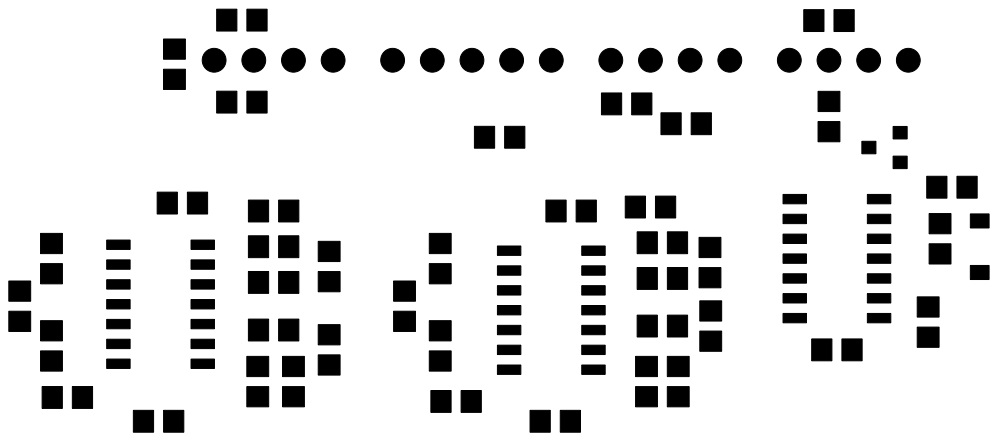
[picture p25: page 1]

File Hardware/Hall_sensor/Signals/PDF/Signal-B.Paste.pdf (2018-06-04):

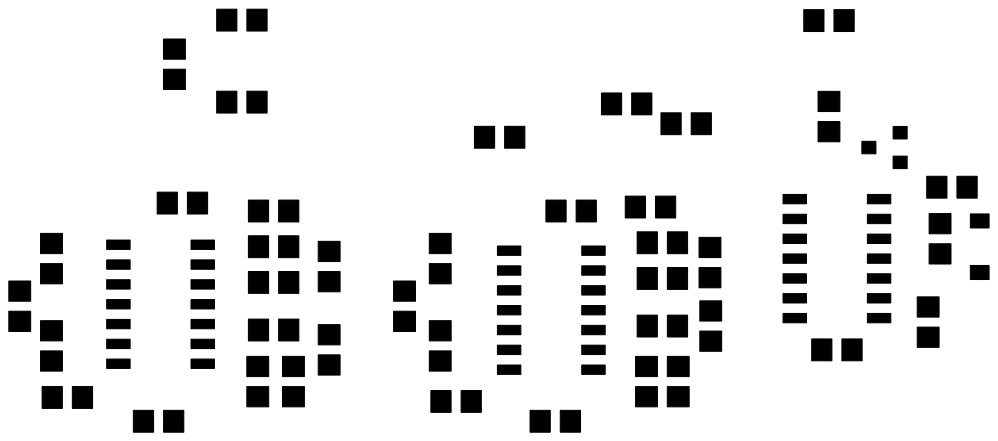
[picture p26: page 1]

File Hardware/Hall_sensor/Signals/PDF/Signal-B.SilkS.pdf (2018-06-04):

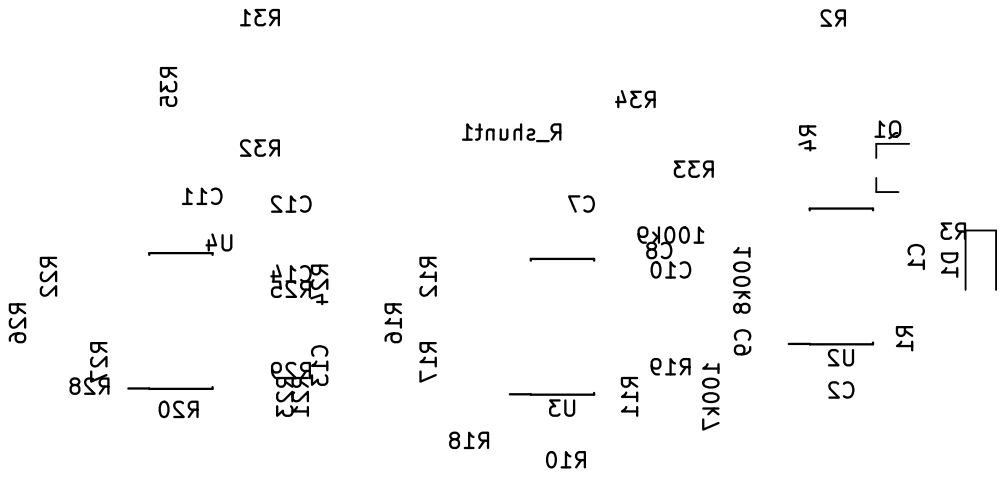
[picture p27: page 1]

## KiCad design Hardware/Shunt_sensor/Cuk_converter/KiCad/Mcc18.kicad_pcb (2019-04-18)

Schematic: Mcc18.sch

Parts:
C1: 1uF; C_2512_6332Metric_Pad1.52x3.35mm_HandSolder
C2, C5, C10: 10uF; C_0805_2012Metric_Pad1.15x1.40mm_HandSolder
C3, C4, C8, C9, C11, C16, C17: 100nF; C_0805_2012Metric_Pad1.15x1.40mm_HandSolder
Cc1, Cc2, Cc3, Cc4, Cc5, Cc6, Cc7, Cc8, Cc9, Cc10, Cc11, Cc12: 1uF 100V; C_1206_3216Metric_Pad1.42x1.75mm_HandSolder
Ci1, Ci2, Ci3: 4,7uF 50V; C_1206_3216Metric_Pad1.42x1.75mm_HandSolder
Co1, Co2, Co3, Co4, Co5: 2.2uF 100V; C_1206_3216Metric_Pad1.42x1.75mm_HandSolder
Cs12, Cs13, Cs14, Cs15: 100nF; C_1206_3216Metric_Pad1.42x1.75mm_HandSolder
D1: 80CPQ150PbF; TO-247-3_Horizontal_TabUp
Ds1, Ds2, Ds3, Ds4: BYD77; D_MELF_Handsoldering
F1: Fuse; Porta_Fusivel
HS1: Heatsink; hs10425
JP1, JP4: VBat-Sen; SolderJumper-2_P1.3mm_Open_Pad1.0x1.5mm
JP5: ON/OFF; TerminalBlock_bornier-2_P5.08mm
L1, L3: L_Small; SolderJumper-2_P1.3mm_Open_Pad1.0x1.5mm
L1/2, L2/2: L_Core_Iron_Small; Inductor_Nocoupled
MK1: Mounting_Hole; MountingHole_2.2mm_M2_Pad
Q1: IRFP4321PbF; TO-247-3_Horizontal_TabUp
R101, R102: 330KR; R_0805_2012Metric_Pad1.15x1.40mm_HandSolder; Tolerance 1%
R103, R110: 100; R_0805_2012Metric_Pad1.15x1.40mm_HandSolder; Tolerance 1%
R105: 47R; R_0805_2012Metric_Pad1.15x1.40mm_HandSolder; Tolerance 1%
Rg1: 10k; R_0805_2012Metric_Pad1.15x1.40mm_HandSolder
Rs2, Rs3, Rs4, Rs5: 100; R_2512_6332Metric_Pad1.52x3.35mm_HandSolder
Rshunt1: 1500uR; PML100HZPJV0L5
Screw1: -P; MountingHole_5mm_Pad
Screw2: +P; MountingHole_5mm_Pad
Screw3: -B; MountingHole_5mm_Pad
Screw4: +B; MountingHole_5mm_Pad
TP1, TP2, TP3, TP4, TP5, TP6, TP7, TP8, TP9, TP10, TP11, TP12, TP13, TP14: TP; TestPoint_Pad_2.0x2.0mm
Tvs1, Tvs2, Tvs4: D_TVS_ALT; D_0805_2012Metric_Castellated
Tvs3: Tvs; D_0805_2012Metric_Castellated
U1: INA240; SOIC-8_3.9x4.9mm_P1.27mm
U2: DRIVER_(INEP); Driver_(INEP)
U3: LM7812_TO220; TO-220-3_Horizontal_TabDown
U4: Signals_MCC; SignalsBarrapinosGrande
U5: ZCS; ZCS18_Handsoldering

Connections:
+5V: C17.1, L1.2, U5.5
+5VA: C11.2, C16.1, L1.1, TP13.1, Tvs3.1, U1.6, U4.17
+12V: C4.1, C5.1, C8.1, L3.1, U3.3 (VO)
/+18V_OUT: C2.1, C3.1, U3.1 (VI), U5.1
/+B: Co1.2, Co2.2, Co3.2, Co4.2, Co5.2, L1/2.2, R103.1, Screw4.1
/+Vp: Cc1.1, Cc2.1, Cc3.1, Cc4.1, Cc5.1, Cc6.1, Cc7.1, Cc8.1, Cc9.1, Cc10.1, Cc11.1, Cc12.1, Ci1.2, Ci2.2, Ci3.2, Cs15.2, Ds3.1, Ds4.2, Q1.2 (D), R102.1, Rs4.2, Screw2.1, TP10.1
/-B: Cc1.2, Cc2.2, Cc3.2, Cc4.2, Cc5.2, Cc6.2, Cc7.2, Cc8.2, Cc9.2, Cc10.2, Cc11.2, Cc12.2, Co1.1, Co2.1, Co3.1, Co4.1, Co5.1, Cs13.1, D1.1, D1.3, Ds1.2, JP1.1, JP4.2, Rs2.2, Screw3.1, TP7.1
/-P_unfused: F1.2, Screw1.1
/-Vp: Ci1.1, Ci2.1, Ci3.1, L2/2.1, R101.1, Rshunt1.1, U1.8
/BatOVInterrupt: U4.14, U5.9
/Gate: Q1.1 (G), Rg1.1, TP12.1, U2.1
/INA240_OUT: R110.1, U1.5
/Ipanel_adc+: C1.1, R110.2, TP4.1, Tvs1.1, U5.32
/PWM: TP14.1, U2.6, U4.15, U5.15
/Rs-: F1.1, Rshunt1.2, U1.1
/Source: Cs12.1, Cs14.1, D1.2, Ds2.2, L1/2.1, L2/2.2, Q1.3 (S), Rg1.2, Rs3.2, Rs5.1, TP6.1, TP11.1, U2.2
/Vb_sen+: R103.2, R105.2, TP1.1, U4.10
/Vb_sen-: JP4.1, R105.1, TP2.1, U4.11
/Vbat_adc+: TP5.1, Tvs2.1, U4.13, U5.33
/Vp_sen+: R102.2, TP9.1, U4.2
/Vp_sen-: R101.2, TP8.1, U4.1
/Vpanel_adc+: TP3.1, Tvs4.2, U4.4, U5.31
GND: C1.2, C2.2, C3.2, C4.2, C5.2, C8.2, C9.2, C10.2, C11.1, C16.2, C17.2, JP1.2, JP5.1, Tvs1.2, Tvs2.2, Tvs3.2, Tvs4.1, U1.2, U1.3, U1.4, U1.7, U2.4, U2.7, U3.2 (GND), U4.3, U4.5, U4.12, U4.16, U5.2, U5.3, U5.4, U5.6, U5.7, U5.8, U5.18, U5.37
unnamed: C9.1, C10.1, L3.2, U2.5
unnamed: Cs12.2, Rs2.1
unnamed: Cs13.2, Ds2.1, Ds3.2, Rs3.1
unnamed: Cs14.2, Ds1.1, Ds4.1, Rs4.1
unnamed: Cs15.1, Rs5.2
unnamed: JP5.2, U5.10

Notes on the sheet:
Driver Supply
Obseravaçoes para a placa definitiva
Verificar Snubber || Colocar Tvs no lugar || Ver qual o footprint dos capacitores || Ver se eu n caguei nada
Current Sensor
Capacitor Bank 12uF 100V
Capacitor Bank 11uF 100V
Arrumar footprint snubber

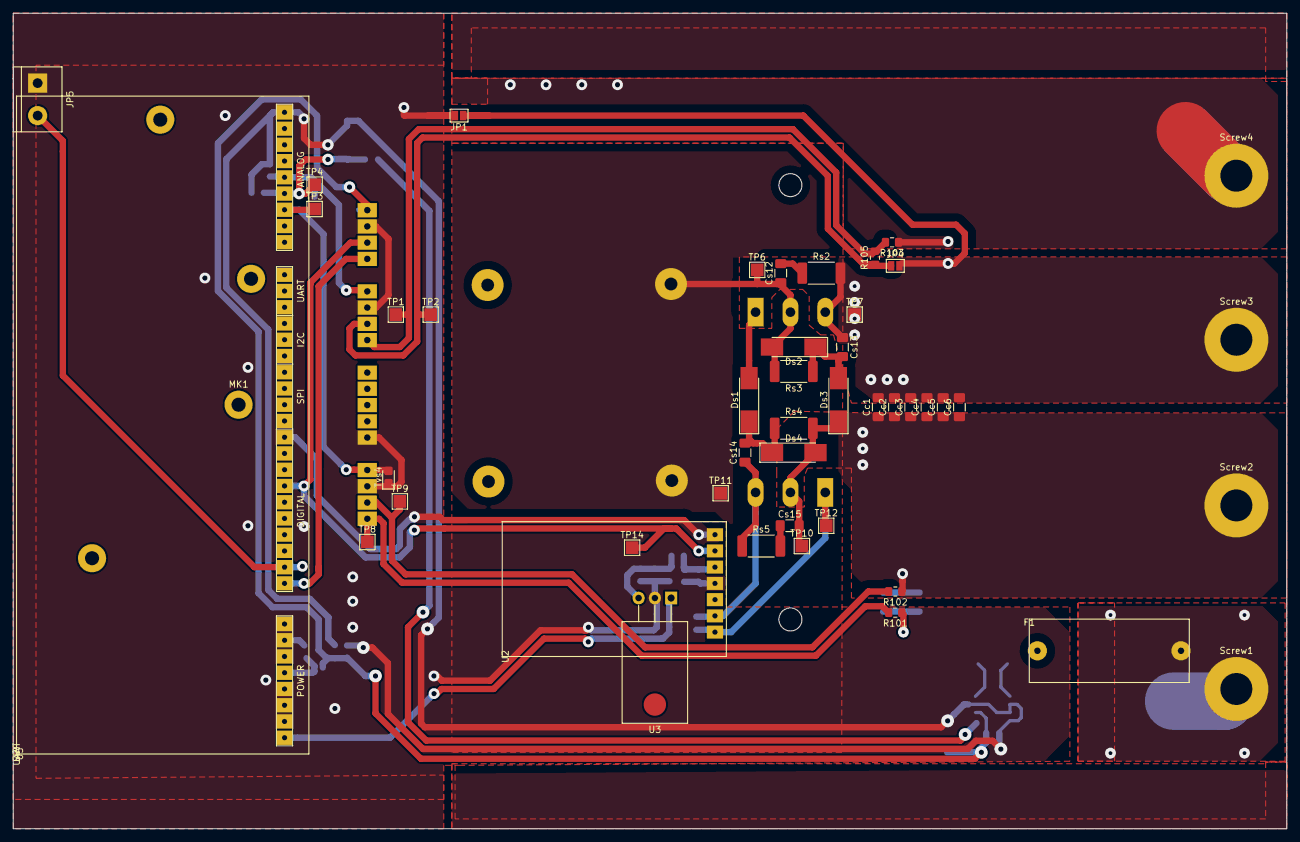
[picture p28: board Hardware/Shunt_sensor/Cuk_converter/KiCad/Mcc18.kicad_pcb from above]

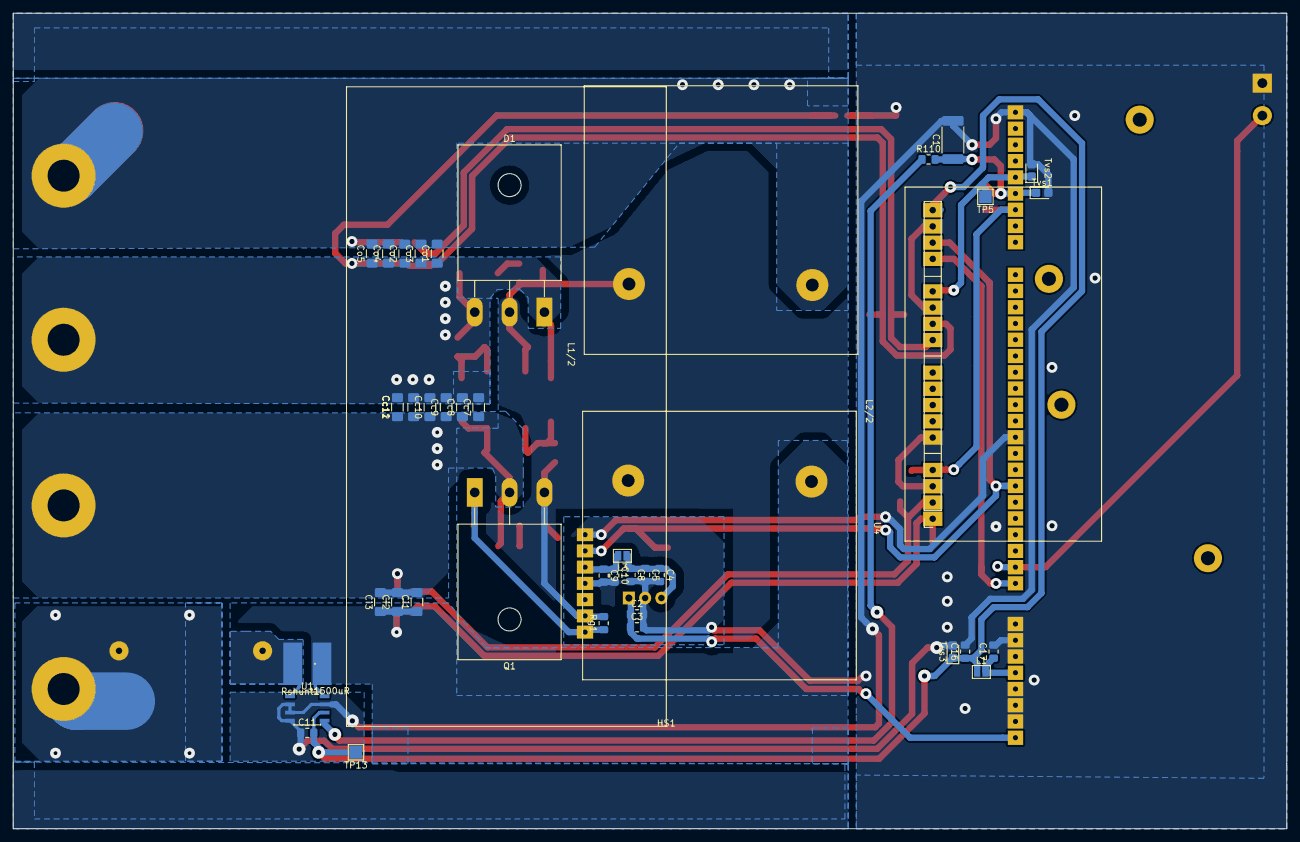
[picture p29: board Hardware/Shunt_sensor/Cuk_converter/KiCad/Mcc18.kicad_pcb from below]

Board: 2 copper layers, 199.1 x 127.5 mm, 89 parts (42 on the bottom side), 29 nets.

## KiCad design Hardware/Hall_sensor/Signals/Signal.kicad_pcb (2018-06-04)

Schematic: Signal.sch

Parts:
100k7: R13; R_0805_2012Metric_Pad1.29x1.40mm_HandSolder
100k8: R14; R_0805_2012Metric_Pad1.29x1.40mm_HandSolder
100k9: R15; R_0805_2012Metric_Pad1.29x1.40mm_HandSolder
C1, C2: C_Small; C_0805_2012Metric_Pad1.29x1.40mm_HandSolder
C7, C11: 100nF; C_0805_2012Metric_Pad1.29x1.40mm_HandSolder
C8, C9, C12, C13: 330p; C_0805_2012Metric_Pad1.29x1.40mm_HandSolder
C10, C14: 47p; C_0805_2012Metric_Pad1.29x1.40mm_HandSolder
D1: MMSZ5230BT1; D_SOD-123
MK1: Mounting_Hole; MountingHole_4mm_Pad_Via
Q1: Q_NPN_Darlington_BEC; SOT-23
R1, R2, R3, R4: R_US; R_0805_2012Metric_Pad1.29x1.40mm_HandSolder
R10, R11, R12, R16, R17, R18, R19, R20, R21, R22, R23, R24, R25, R26, R27, R28, R29: 100k; R_0805_2012Metric_Pad1.29x1.40mm_HandSolder
R31, R32, R33, R34, R35: ??; R_0805_2012Metric_Pad1.29x1.40mm_HandSolder
R_shunt1: 100k; R_0805_2012Metric_Pad1.29x1.40mm_HandSolder
U1: Signals_MCC; Signals
U2, U3, U4: LM324; SOIC-14_3.9x8.7mm_P1.27mm

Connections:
+5VA: C2.1, C7.2, C11.2, R1.2, U1.17, U2.4 (V+), U3.4 (V+)
/+3.9V: C1.1, D1.1, R1.1, U2.9 (-)
/BatOVInterrupt: R2.2, R3.1, U1.14, U2.8
/Ipanel: C8.1, U1.9, U3.8, U3.9 (-)
/Ipanel_Ref: R_shunt1.1, U1.7, U3.5 (+)
/Ipanel_SIG: R_shunt1.2, U1.6, U3.3 (+)
/PWM: R4.1, U1.15
/Vbat: U1.13, U2.6 (-), U2.7
/Vbat_SIG_IN: R34.2, U1.10
/Vpanel: C12.2, U1.4, U4.8, U4.9 (-)
/Vpanel_Ref: R32.1, R35.2, U1.1, U4.5 (+)
/Vpanel_SIG: R31.2, R35.1, U1.2, U4.3 (+)
GNDA: C1.2, C2.2, C7.1, C9.1, C10.1, C11.1, C13.1, C14.1, D1.2, Q1.2, R2.1, R19.2, R29.2, R31.1, R32.2, R33.2, U1.3, U1.5, U1.8, U1.11, U1.12, U1.16, U2.3 (+), U2.11 (V-), U2.12 (+), U3.11 (V-), U4.11 (V-)
unnamed: 100k7.1, R11.2, U3.14
unnamed: 100k7.2, 100k8.1, C9.2
unnamed: 100k8.2, 100k9.1, C8.2
unnamed: 100k9.2, C10.2, U3.10 (+)
unnamed: C12.1, R24.1, R25.2
unnamed: C13.2, R23.1, R24.2
unnamed: C14.2, R25.1, U4.10 (+)
unnamed: Q1.1, R3.2
unnamed: Q1.3, R4.2
unnamed: R10.1, R12.1, U3.7
unnamed: R10.2, R11.1, U3.13 (-)
unnamed: R12.2, R16.1, U3.6 (-)
unnamed: R16.2, R17.1, U3.2 (-)
unnamed: R17.2, R18.1, U3.1
unnamed: R18.2, R19.1, U3.12 (+)
unnamed: R20.1, R21.2, U4.13 (-)
unnamed: R20.2, R22.1, U4.7
unnamed: R21.1, R23.2, U4.14
unnamed: R22.2, R26.1, U4.6 (-)
unnamed: R26.2, R27.2, U4.2 (-)
unnamed: R27.1, R28.2, U4.1
unnamed: R28.1, R29.1, U4.12 (+)
unnamed: R33.1, R34.1, U2.5 (+), U2.10 (+)
unnamed: U2.1, U2.2 (-)
unnamed: U2.13 (-), U2.14

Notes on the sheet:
To bypass this instrumentation amplifier: 5 shorts 11 and 3 shorts 8.
3rd order Sallen-Key Low-Pass filter at 2728kHz
This signal is a current up to 12.5mA. 120 Ohms will produce 1.5V. It means that this overall bock needs to have a gain of 2 to produce 3V for the microcontroller.

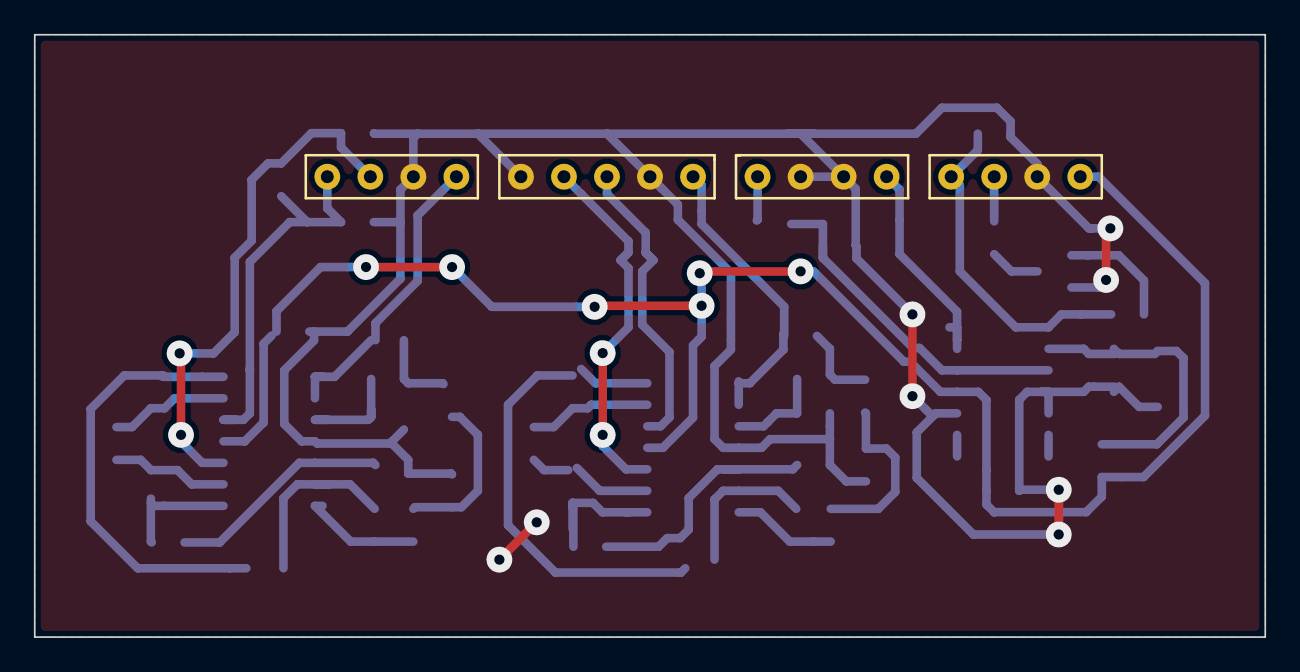
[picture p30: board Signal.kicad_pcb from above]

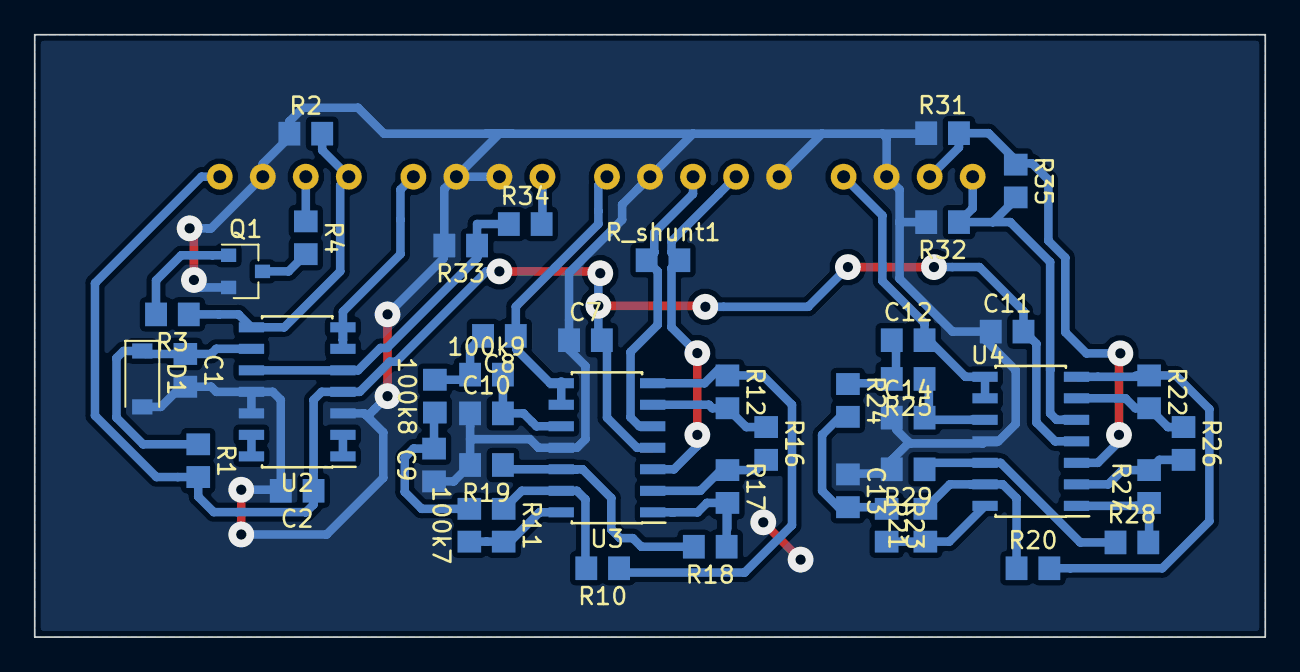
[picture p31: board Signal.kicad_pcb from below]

Board: 2 copper layers, 72.6 x 35.6 mm, 46 parts (45 on the bottom side), 38 nets.

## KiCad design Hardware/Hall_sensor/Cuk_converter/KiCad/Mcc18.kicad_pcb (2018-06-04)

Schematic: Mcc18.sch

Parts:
C1, C3, C4, C6, C7, C8, C9: 100nF; C_0805_2012Metric_Pad1.29x1.40mm_HandSolder
C2, C5, C10: 10uF; C_0805_2012Metric_Pad1.29x1.40mm_HandSolder
Cc1, Cc2, Cc3, Cc4: 6.8uF; C_Rect_L29.0mm_W11.9mm_P27.50mm_MKT
Ci1, Ci2, Ci3: 4.7uF; C_Rect_L16.5mm_W9.2mm_P15.00mm_MKT
Co1, Co2, Co3: 4.7uF; C_Rect_L29.0mm_W11.9mm_P27.50mm_MKT
Cs1, Cs2, Cs3, Cs4: ??; C_1206_3216Metric_Pad1.39x1.80mm_HandSolder; Voltage 200V; Tolerance 10%
D1: 80CPQ150PbF; TO-247-3_Horizontal_TabUp
Ds1, Ds2: BYD77; D_MELF_Handsoldering
F1: Fuse; Porta_Fusivel
HS1: Heatsink; hs10425
L1: 50uH/50uH; NEE-42-20-DE
L2, L3: L_Small; L_0805_2012Metric_Pad1.29x1.40mm_HandSolder
Q1: IRFP4321PbF; TO-247-3_Horizontal_TabUp
R1: 10k; R_0805_2012Metric_Pad1.29x1.40mm_HandSolder
R101, R102, R103, R104: ??; R_0805_2012Metric_Pad1.29x1.40mm_HandSolder; Tolerance 1%
R105, R106: 0R; R_0805_2012Metric_Pad1.29x1.40mm_HandSolder; Tolerance 1%
Rs1, Rs4: ??; R_2512_6332Metric_Pad1.49x3.40mm_HandSolder; Tolerance 10%
Rs2, Rs3: ??; R_2512_6332Metric_Pad1.49x3.40mm_HandSolder
Screw1: -P; MountingHole_5mm_Pad
Screw2: +P; MountingHole_5mm_Pad
Screw3: -B; MountingHole_5mm_Pad
Screw4: +B; MountingHole_5mm_Pad
U1: LTSP_25-NP
U2: DRIVER_(INEP); Driver_(INEP)
U3: LM7812_TO220; TO-220-3_Horizontal_TabDown
U4: Signals_MCC; Signals
U5: ZCS; ZCS18

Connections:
+5V: C1.2, C7.1, L2.2, U1.7, U5.5
+5VA: C6.1, L2.1, U4.17
+12V: C4.1, C5.1, C8.1, L3.1, U3.3 (VO)
/+18V_OUT: C2.1, C3.1, U3.1 (VI), U5.1
/+B: Co1.1, Co2.1, Co3.1, L1.3, R103.1, Screw4.1
/+Ip: R105.1, U1.9
/+Vp: Cc1.2, Cc2.2, Cc3.2, Cc4.2, Ci1.2, Ci2.2, Ci3.2, D1.1, D1.3, Ds1.2, R102.1, Rs1.2, Rs3.2, Screw2.1
/-B: Cc1.1, Cc2.1, Cc3.1, Cc4.1, Co1.2, Co2.2, Co3.2, Ds2.2, Q1.2 (D), R104.1, Rs2.2, Rs4.2, Screw3.1
/-P_unfused: F1.2, Screw1.1
/-Vp: Ci1.1, Ci2.1, Ci3.1, F1.1, R101.1, U1.4
/BatOVInterrupt: U4.14, U5.9
/Gate: Q1.1 (G), R1.2, U2.1
/Ip_sen+: R105.2, U4.6
/Ip_sen-: R106.2, U4.7
/Ipanel_adc+: U4.9, U5.32
/PWM: U2.6, U4.15, U5.15
/Source: Cs1.2, Cs2.2, Cs3.2, Cs4.2, D1.2, L1.2, L1.4, Q1.3 (S), R1.1, U2.2
/Vb_sen+: R103.2, U4.10
/Vb_sen-: R104.2, U4.11
/Vbat_adc+: U4.13, U5.33
/Vp_sen+: R102.2, U4.2
/Vp_sen-: R101.2, U4.1
/Vpanel_adc+: U4.4, U5.31
GND: C1.1, C2.2, C3.2, C4.2, C5.2, C7.2, C8.2, C9.2, C10.2, R106.1, U1.8, U2.4, U2.7, U3.2 (GND), U5.3, U5.7, U5.18
GNDA: C6.2, U4.3, U4.5, U4.8, U4.12, U4.16, U5.37
unnamed: C9.1, C10.1, L3.2, U2.5
unnamed: Cs1.1, Rs1.1
unnamed: Cs2.1, Ds1.1, Rs2.1
unnamed: Cs3.1, Ds2.1, Rs3.1
unnamed: Cs4.1, Rs4.1
unnamed: L1.1, U1.1, U1.2
unnamed: U1.3, U1.5, U1.6

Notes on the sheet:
In this config (2 turns) it senses up to 12.5A
CurrentSense
Driver Supply
Snubber
Obseravaçoes para a placa definitiva
Adicionar um divisor de tensão na medida de tensão da batria e painel , para que seja mais seguro

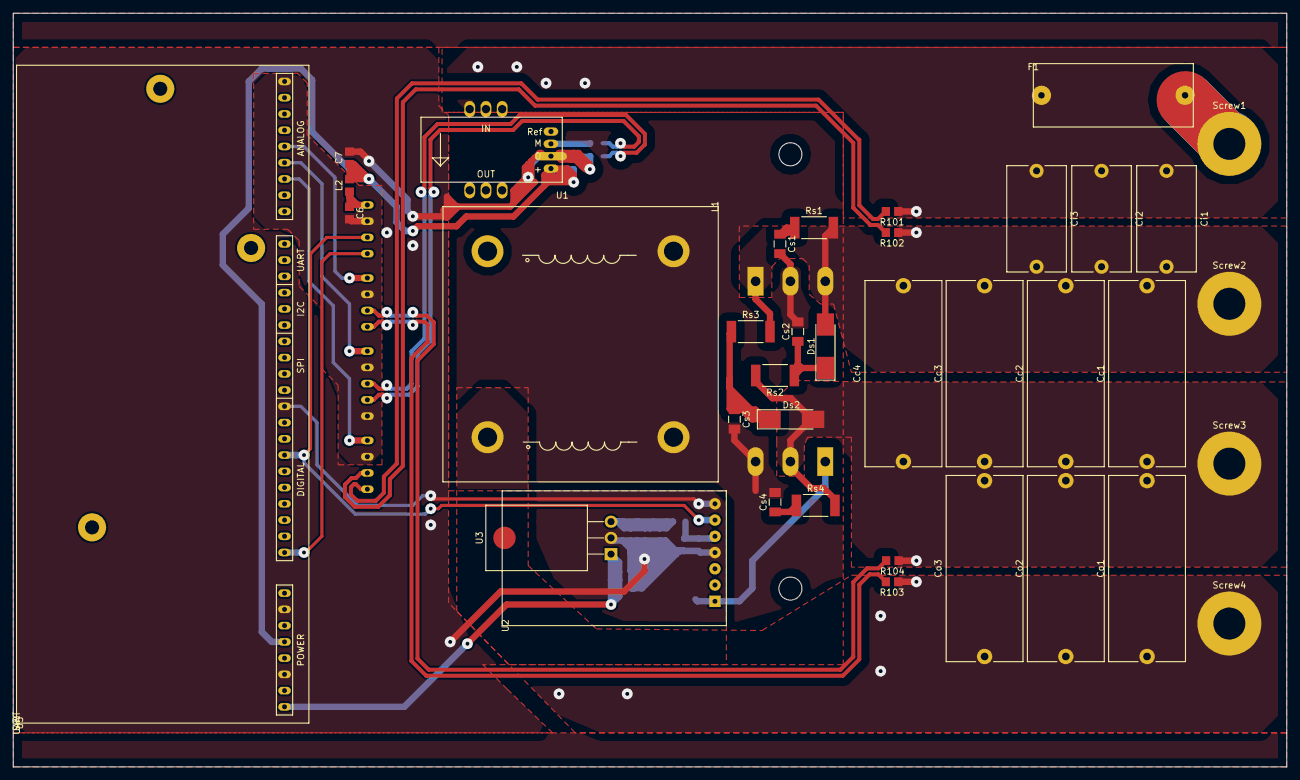
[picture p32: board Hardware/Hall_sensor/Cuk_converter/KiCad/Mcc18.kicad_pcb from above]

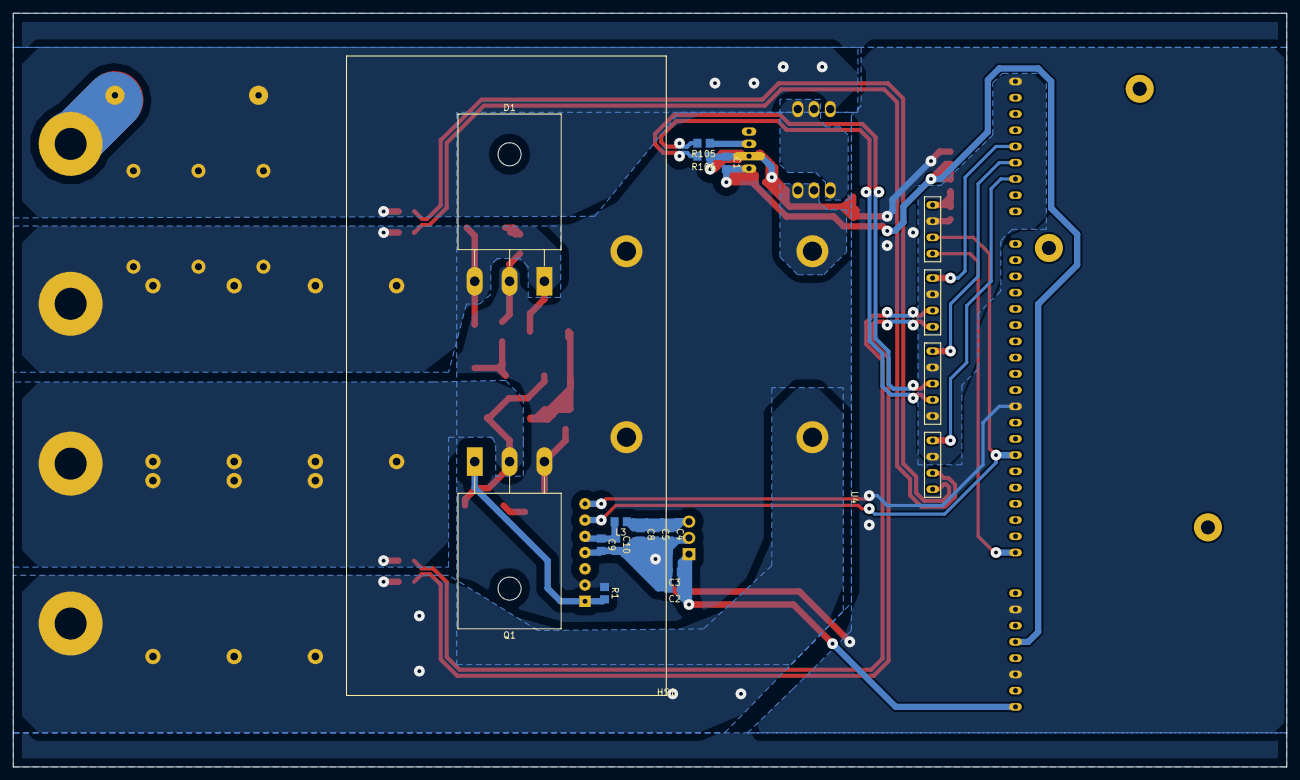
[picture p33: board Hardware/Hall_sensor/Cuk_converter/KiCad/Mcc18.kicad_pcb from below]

Board: 2 copper layers, 199.1 x 117.9 mm, 53 parts (16 on the bottom side), 32 nets.

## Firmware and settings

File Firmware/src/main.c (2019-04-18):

// coding: utf-8

#include "main.h"

int main(void)
{
    #ifdef USART_ON
        usart_init(MYUBRR,1,1);                         // inicializa a usart
        VERBOSE_MSG_INIT(usart_send_string("\n\n\nUSART... OK!\n"));
    #endif

    _delay_ms(1000);

    #ifdef PWM_ON
        VERBOSE_MSG_INIT(usart_send_string("PWM..."));
        pwm_init();
        VERBOSE_MSG_INIT(usart_send_string(" OK!\n"));
    #else
        VERBOSE_MSG_INIT(usart_send_string("PWM... OFF!\n"));
    #endif

    #ifdef CAN_ON
        VERBOSE_MSG_INIT(usart_send_string("CAN (500kbps)..."));
        can_init(BITRATE_500_KBPS);
        VERBOSE_MSG_INIT(usart_send_string(" OK!\n"));
        VERBOSE_MSG_INIT(usart_send_string("CAN filters..."));
        //can_static_filter(can_filter);
        VERBOSE_MSG_INIT(usart_send_string(" OK!\n"));
    #else
        VERBOSE_MSG_INIT(usart_send_string("CAN... OFF!\n"));
    #endif

    #ifdef ADC_ON
        VERBOSE_MSG_INIT(usart_send_string("ADC..."));
        adc_init();
        VERBOSE_MSG_INIT(usart_send_string(" OK!\n"));
    #else
        VERBOSE_MSG_INIT(usart_send_string("ADC... OFF!\n"));
    #endif

    #ifdef SLEEP_ON 
        VERBOSE_MSG_INIT(usart_send_string("SLEEP..."));
        sleep_init();
        VERBOSE_MSG_INIT(usart_send_string(" OK!\n"));
    #else
        VERBOSE_MSG_INIT(usart_send_string("SLEEP... OFF!\n"));
    #endif

    #ifdef WATCHDOG_ON
        VERBOSE_MSG_INIT(usart_send_string("WATCHDOG..."));
        wdt_init();
        VERBOSE_MSG_INIT(usart_send_string(" OK!\n"));
    #else
        VERBOSE_MSG_INIT(usart_send_string("WATCHDOG... OFF!\n"));
    #endif

 	#ifdef MACHINE_ON
        VERBOSE_MSG_INIT(usart_send_string("MACHINE..."));
		machine_init();
        VERBOSE_MSG_INIT(usart_send_string(" OK!\n"));
    #else
        VERBOSE_MSG_INIT(usart_send_string("MACHINE... OFF!\n"));
	#endif
	
    #ifdef LED_ON
        set_bit(LED_DDR, LED);                      // LED como saída
        VERBOSE_MSG_INIT(usart_send_string("LED... OK!\n"));
    #else
        VERBOSE_MSG_INIT(usart_send_string("LED... OFF!\n"));
    #endif

	/*
    // ------------------------------------------------------------------------
	clr_bit(BatOverVoltageInterrupt_DDR,BatOverVoltageInterrupt);	// BatOverVoltageInterrupt como entrada
	
	clr_bit(Enable_DDR,Enable);					// Enable como entrada
	set_bit(Enable_PORT,Enable);				// Enable com pull-up
	
	// interrupcao do Enable (Enable PD3)
    set_bit(EICRA, ISC11);                      // falling edge for int1
    set_bit(EIMSK, INT1);                       // enables int1 interrupt
    set_bit(EIFR, INTF1);                       // clears int1 interrupt
	
	// interrupcao Over voltage Battery (BatOvervoltage_interrupt PD2)
	set_bit(EICRA, ISC10);                      // rising edge for int1
	set_bit(EIMSK, INT0);                       // enables int1 interrupt
	set_bit(EIFR, INTF0);                       // clears int0 interrupt
	*/	
    
    // reset as input pull-up against noise
    clr_bit(DDRC, PC6);
    set_bit(PORTC, PC6);
	
    sei();
	
	for(;;){
		#ifdef WATCHDOG_ON
            wdt_reset();
		#endif

        #ifdef MACHINE_ON
            machine_run();
        #else
            #ifdef PWM_ON
                #ifdef PWM_TEST
                    #ifdef CONVERTER_TEST_WITH_FIXED_DUTYCYCLE
                        set_pwm_duty_cycle(CONVERTER_TEST_WITH_FIXED_DUTYCYCLE_DT_VALUE);
                    #else
                        static uint8_t i = 0;
                        set_pwm_duty_cycle(i++);
                        if(i>PWM_D_MAX) i = PWM_D_MIN;
                    #endif
                #else
                    #ifdef PEO_TEST
                        read_and_check_adcs();
                        pwm_compute();
                    #endif
                #endif
            #endif
        #endif

		#ifdef SLEEP_ON
            sleep_mode();
		#endif
	}
}


/**
 * @brief se em debug, fica chaveando os pinos de debugs até o reset do watchdog
 */
ISR(BADISR_vect)
{
    for(;;){
        VERBOSE_MSG_ERROR(usart_send_string("\nFATAL ERROR: BAD ISR."));
        #ifdef WATCHDOG_ON
            VERBOSE_MSG_ERROR(usart_send_string("WAITING FOR WATCHDOG TO RESET...\n"));
        #endif
        #ifdef DEBUG_ON
            DEBUG0;
            DEBUG1;
            _delay_ms(100);
        #endif
    }
}

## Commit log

2018-05-26 create signals directory
    [Mcc18.kicad_pcb, Mcc18.sch]
2018-05-26 snubber update
    [Mcc18.kicad_pcb, Mcc18.sch]
2018-05-26 Snubber finished
    [Mcc18.kicad_pcb]
2018-05-26 Add cut board layer
    [Mcc18.kicad_pcb]
2018-05-26 add a fill zone witout net
    [Mcc18.kicad_pcb]
2018-05-27 Fixed errors
    [Mcc18.kicad_pcb, Mcc18.sch]
2018-05-28 created signals PCB
    [Mcc18.kicad_pcb, Mcc18.sch, Signal.kicad_pcb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]
2018-05-28 created BOM of materials
    [Mcc18.kicad_pcb, Mcc18_bom_.ods]
2018-05-29 .wrl added, library link paths fixed
    [Mcc18.sch]
2018-05-30 rework on snubber routing
    [Mcc18.kicad_pcb, Mcc18.sch]
2018-05-30 PCB Reworked
    [Mcc18.kicad_pcb, Mcc18.sch]
2018-05-30 Files to fabrication exported
    [Mcc18-B.Adhes.gbr, Mcc18-B.CrtYd.gbr, Mcc18-B.Cu.gbr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]
2018-05-30 minor fixes and added IMG folder
    [Mcc18-B.Adhes.gbr, Mcc18-B.CrtYd.gbr, Mcc18-B.Cu.gbr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]
2018-05-30 pads and traces of current sensor supply fixed
    [Mcc18.kicad_pcb]
2018-05-30 minor fixes
    [Mcc18-B.Adhes.gbr, Mcc18-B.CrtYd.gbr, Mcc18-B.Cu.gbr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]
2018-05-30 diff pairs locked
    [Mcc18.kicad_pcb]
2018-05-30 some zones fix
    [Mcc18-B.Adhes.gbr, Mcc18-B.CrtYd.gbr, Mcc18-B.Cu.gbr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]
2018-05-30 minor fixes. GERBERS updated
    [Mcc18-B.Adhes.gbr, Mcc18-B.CrtYd.gbr, Mcc18-B.Cu.gbr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]
2018-05-30 Signals revisado. Foram reduzidos os jjumpers, GERBERS gerados e .wrl exportado.
    [Signal-B.Cu.gbr, Signal-B.Mask.gbr, Signal-B.Paste.gbr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]
2018-05-30 Atualizado 3D do signals para .wrl
    [Mcc18.kicad_pcb]
2018-05-30 power trace optimized
    [Mcc18.kicad_pcb]
2018-05-31 created shunt sensor PCB
    [Mcc18-B.Adhes.gbr, Mcc18-B.CrtYd.gbr, Mcc18-B.Cu.gbr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]
2018-05-31 ok. Now it is on 25~50mils grid.
    [Mcc18.sch]
2018-06-01 finished the first version
    [Mcc18.kicad_pcb, Mcc18.sch]
2018-06-01 fixed clearance
    [Mcc18.kicad_pcb]
2018-06-01 fixed shunt tracks and added 3d images
    [Mcc18.kicad_pcb]
2018-06-03 Added signals PCB Added signals PCB for shunt current sense
    [Signal.kicad_pcb, Signal.sch, Signal1.FCStd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]
2018-06-03 Fixed voltage divider The old voltage divider isn't differential
    [Signal.kicad_pcb, Signal.sch]
2018-06-03 Added signals 3D in cuk PCB _Added signals 3D in signals component in MCCshunt Library._ _Added pin socket in the signals component_ _Added signals component in cuk converter PCB_ _Added MountingHole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
    [Mcc18.kicad_pcb, Mcc18.sch]
2018-06-03 Genereted fabrication files to the Shunt sensor _Generated signals GERBER_ _Generated signals drill_ _Generated signals 3D Images_ _Generated signals PDF_ _Generated Cuk converter GERBER_ _Generated 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
    [Mcc18-B.Adhes.gbr, Mcc18-B.CrtYd.gbr, Mcc18-B.Cu.gbr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]
2018-06-03 Updated fabrication outputs _Updated shunt signals PDF schematic,PDF PCB, GERBER PCB,Drill PCB_ _Updated shunt cuk PDF schematic,PDF PCB, GERBER PCB,Drill PCB_ _Updated hall signals PDF schematic,PDF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
    [Mcc18-B.Adhes.gbr, Mcc18-B.CrtYd.gbr, Mcc18-B.Cu.gbr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]
2018-06-03 generated drill map and report file
    [Mcc18.kicad_pcb]
2018-06-03 shunt signals updated
    [Signal-B.Adhes.gbr, Signal-B.CrtYd.gbr, Signal-B.Cu.gbr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]
2018-06-03 Modified Angled 3D IMG to Shunt cuk
    [Signal.kicad_pcb]
2018-06-04 Replaced all spaces to "_"
    [Mcc18-B.Adhes.gbr, Mcc18-B.CrtYd.gbr, Mcc18-B.Cu.gbr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]
2018-06-04 fixed and created all Fabrication files
    [Mcc18-B.Adhes.gbr, Mcc18-B.CrtYd.gbr, Mcc18-B.Cu.gbr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]
2018-06-06 Basic simulations with shunt added
    [INA211.DSN]
2018-06-06 sensors fixed on simulation. Everything seems working fine
2018-06-22 Added simulation (LTspice) for input voltage measurement.
2018-07-20 Status led changed to new pin and added a blink pattern to main loop if MACHINE_ON isnt defined.
2018-07-20 ADC setted to 5kHz, some other minor improvements.
2018-07-20 USART, WATCHDOG, PWM, ADC working. Now testing machine
2018-07-20 ADC readings tested, ifdefs 8bits fixed
2018-07-20 ADC tested: OK. Reading 1021 at 5V, 0 at 0V
2018-07-22 PWM changed to mode 14 to get better resolution for 100kHz.
2018-07-22 added a print version for 32 bits unsigned
2018-07-30 Added precompiled PWM configurations. Tested -> OK
2018-08-22 Initialized de final version
    [INA211.DSN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]
2018-08-23 Added snubber and driver
    [Mcc18-B.Adhes.gbr, Mcc18-B.CrtYd.gbr, Mcc18-B.Cu.gbr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]
2018-08-23 Finlized signals basic routing
    [Mcc18.kicad_pcb, Mcc18.sch]
2018-08-23 Added ADC tracks
    [Mcc18.kicad_pcb]
2018-08-24 Some 3D added, power reworked to minimize stray inductances
    [Mcc18.kicad_pcb, Mcc18.sch]
2018-08-24 adc_data_ready initialized in adc_init instead adc.h
2018-08-24 algorithm for zero power detection enhanced
2018-08-25 machine prints was causing clock conflict. Fixed
2018-08-25 Added fill zones
    [Mcc18.kicad_pcb, Mcc18.sch]
2018-08-30 Finalized first version PCB
    [Mcc18.kicad_pcb, Mcc18.sch, Mcc18_bom_.ods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]
2018-08-31 final adjusted for cnc.
    [Mcc18.kicad_pcb, Mcc18.sch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]
2018-08-31 Fixed signals tracks
    [Mcc18.sch]

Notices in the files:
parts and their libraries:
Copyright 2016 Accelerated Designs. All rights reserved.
